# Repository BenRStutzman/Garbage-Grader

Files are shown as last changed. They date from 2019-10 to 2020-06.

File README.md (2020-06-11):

# Garbage Grader

Uses machine learning to score plates of food waste in real time.

Project with Austin Engle for Senior Design.

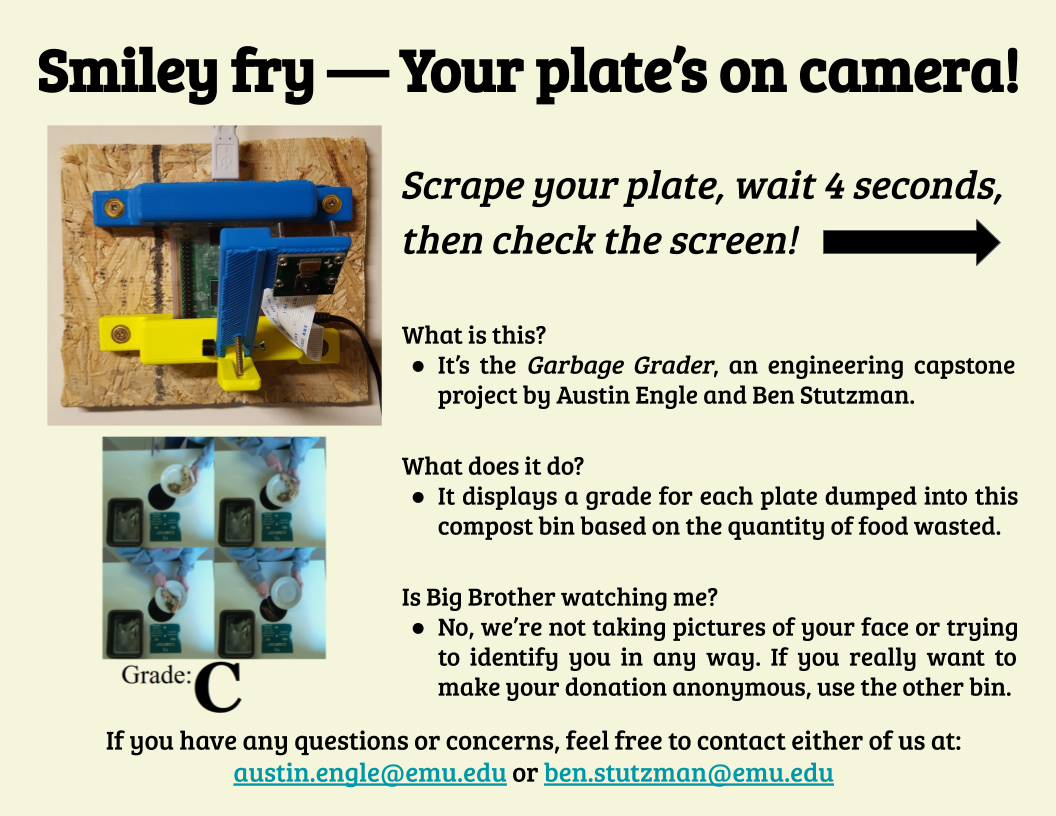
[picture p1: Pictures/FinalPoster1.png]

Poster hanging above the compost bin in EMU's cafeteria
<br><br>
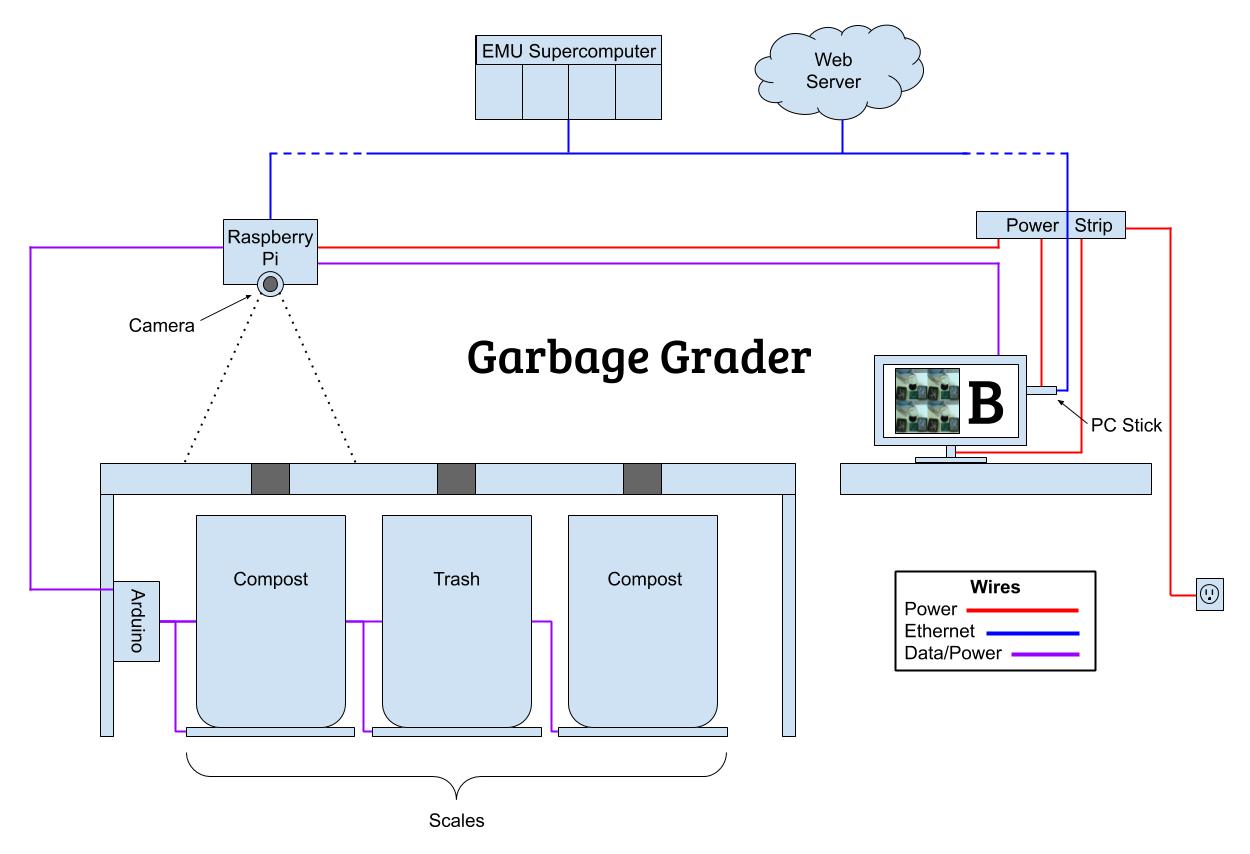
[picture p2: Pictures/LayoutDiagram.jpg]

Overall layout
<br><br>
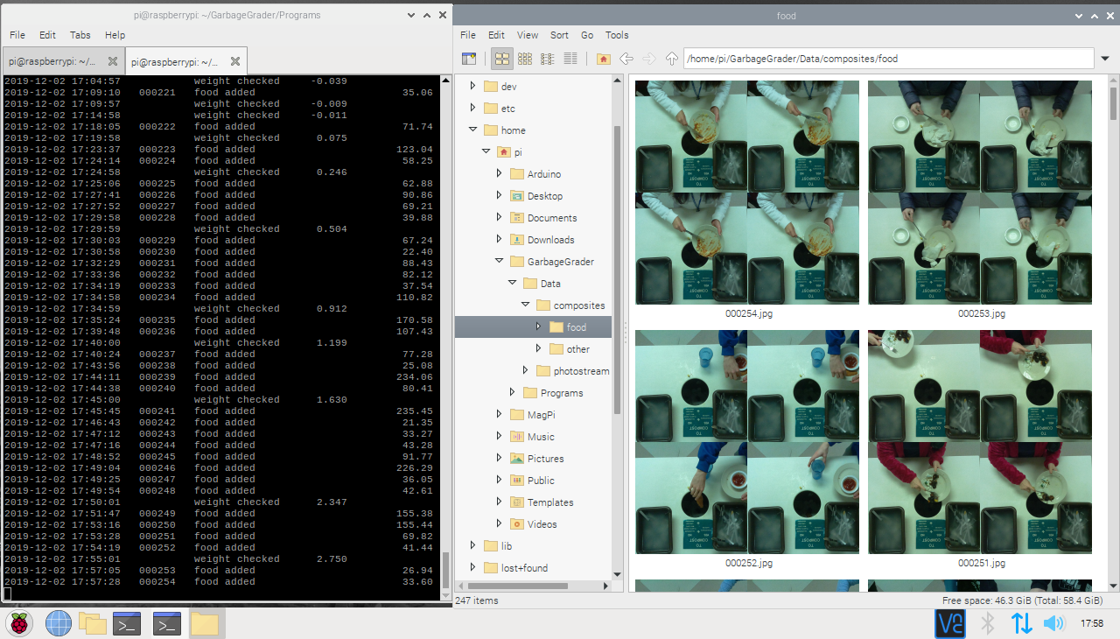
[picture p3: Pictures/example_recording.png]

Raspberry Pi recording pictures of each plate
<br><br>
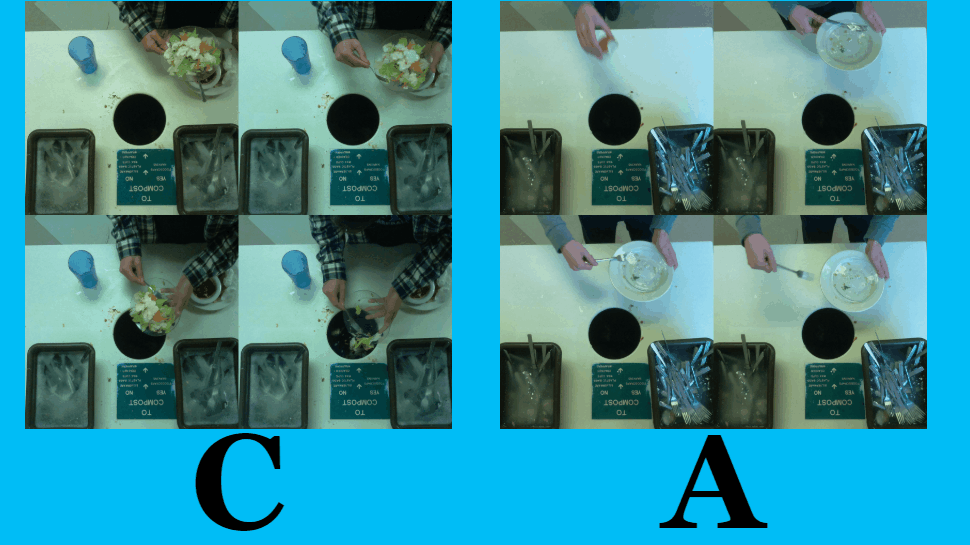
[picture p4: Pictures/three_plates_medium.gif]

Example of TV display as plates are scraped into the compost

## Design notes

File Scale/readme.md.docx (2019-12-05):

To get the arduino code working for the scale, you need to download the hx711 library first. Go to Tools -> mangage libraries -> search for ‘hx711’ and the result should look like this:

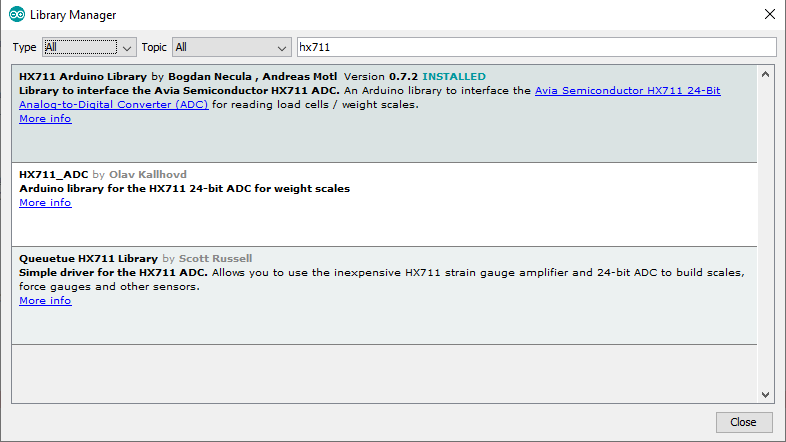
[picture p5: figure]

Select the circled one.

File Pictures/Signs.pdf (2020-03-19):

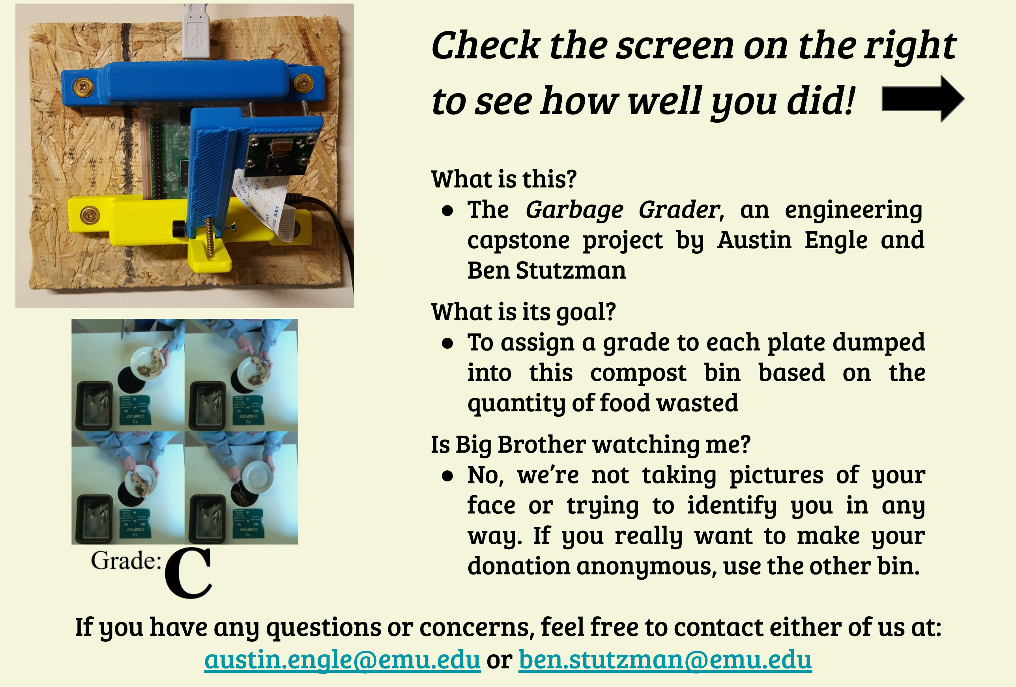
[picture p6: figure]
What is this? ● The Garbage Grader, an engineering capstone project by Austin Engle and Ben Stutzman What is its goal?; into this compost bin based on the quantity of food wasted Is Big Brother watching me? ● No, we’re not taking pictures of your face or trying to identify you in any way. If you really want to make your donation anonymous, use the other bin.; Check the screen on the right to see how well you did!

- To assign a grade to each plate dumped

If you have any questions or concerns, feel free to contact either of us at: austin.engle@emu.edu or ben.stutzman@emu.edu

# Smiley fry — Your plate’s on camera!

- You’ll get a letter grade based on how wasteful our artificial intelligence model thinks your plate was.
- A is the best (no unnecessary waste) and
F is the worst (way too much waste).
- Our model counts all avoidable waste it sees in the picture, including leftover drinks and excess napkins.
- It’s not perfect, but about 93% of the grades it gives are within one letter of what a human would say—and we’re working on improving it.
- If you’re disappointed with your grade:

## Consider taking less food next time!

If you have any questions or concerns, feel free to contact either of us at: austin.engle@emu.edu or ben.stutzman@emu.edu

# What does my grade mean?

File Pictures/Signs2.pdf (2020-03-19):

What is this?
- It’s the Garbage Grader, an engineering capstone project by Austin Engle and Ben Stutzman.

What does it do?
- It displays a grade for each plate dumped into this compost bin based on the quantity of food wasted.

Is Big Brother watching me?
- No, we’re not taking pictures of your face or trying to identify you in any way. If you really want to make your donation anonymous, use the other bin. If you have any questions or concerns, feel free to contact either of us at: austin.engle@emu.edu or ben.stutzman@emu.edu

# Smiley fry — Your plate’s on camera!

Scrape your plate, wait 4 seconds,

### then check the screen!

- You get a letter grade based on how wasteful our artificial intelligence model thinks your plate was.
- A is the best (no unnecessary waste) and
F is the worst (way too much waste).
- Our model counts all avoidable waste it sees in the picture, including leftover drinks and excess napkins.
- It’s not perfect, but about 93% of the grades it gives are within one letter of what a human would say—and we’re working on improving it.
- To improve your grade next time:

## Clean your plate really well

or

## Consider taking less food!

If you have any questions or concerns, feel free to contact either of us at: austin.engle@emu.edu or ben.stutzman@emu.edu

# What does my grade mean?

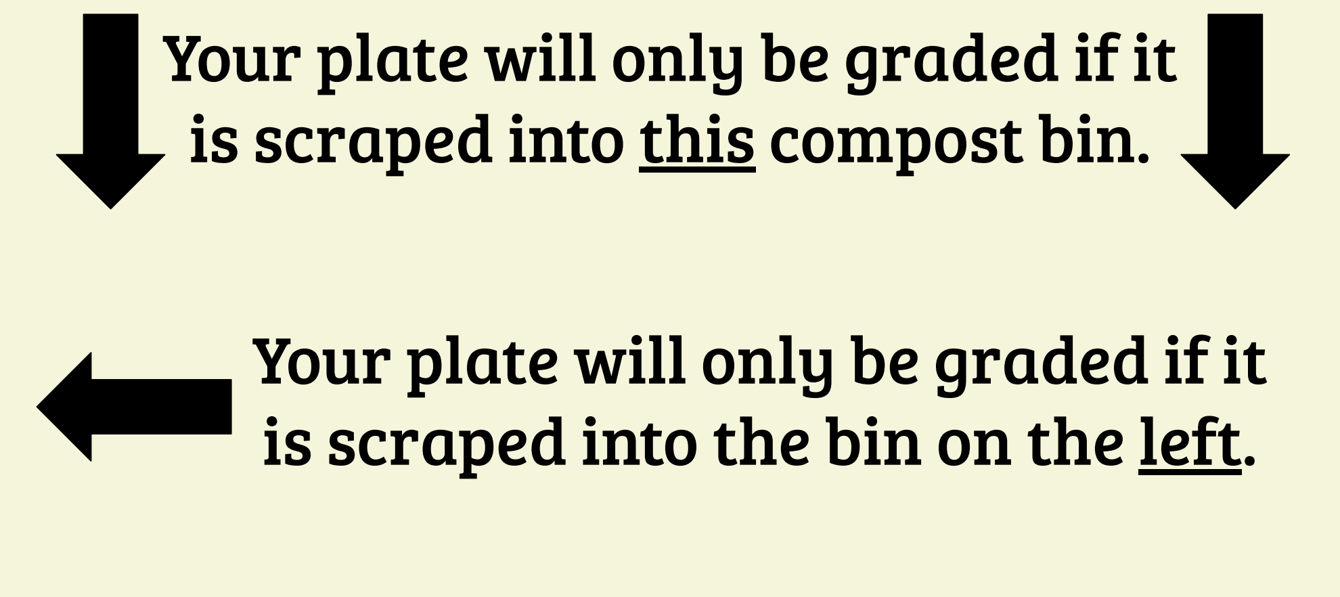
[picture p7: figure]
Your plate will only be graded if it is scraped into this compost bin.; Your plate will only be graded if it is scraped into the bin on the left.

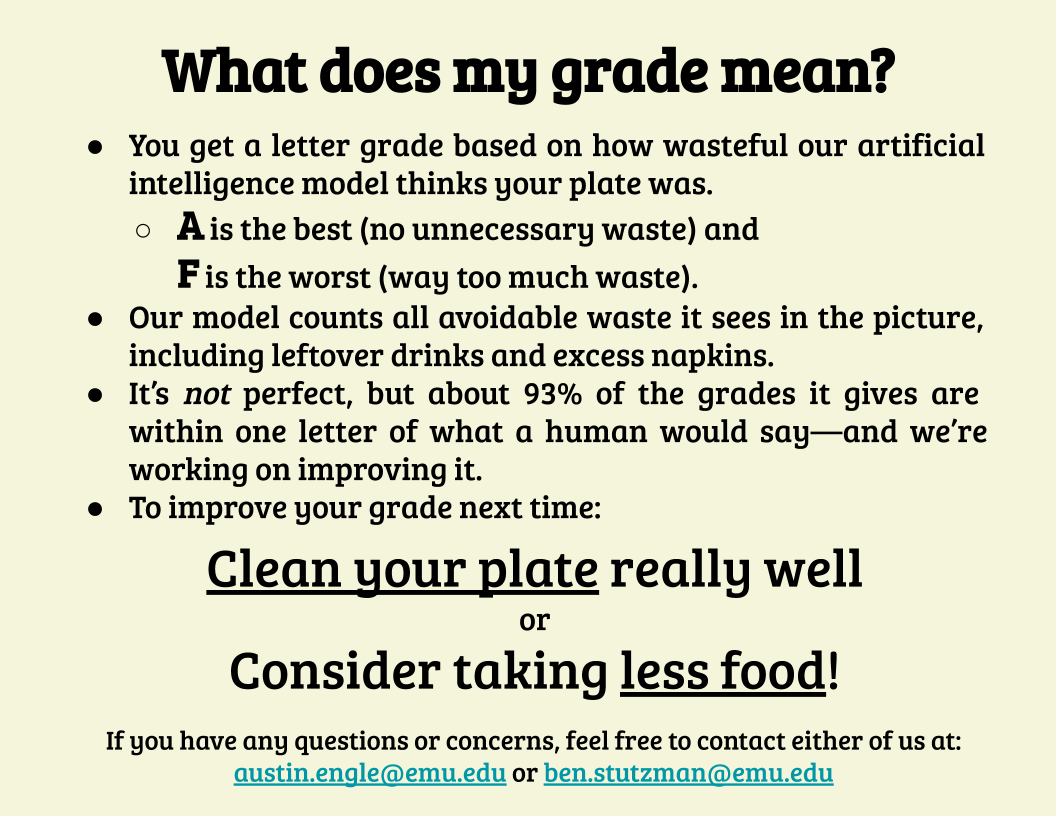
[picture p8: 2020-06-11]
Pictures/FinalPoster2.png

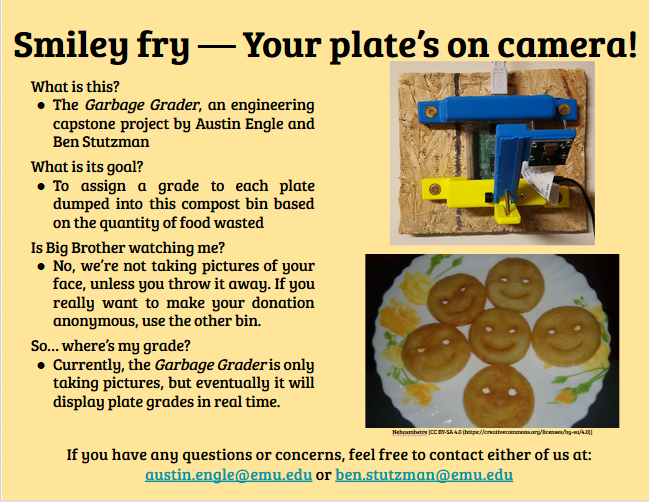
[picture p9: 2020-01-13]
Pictures/poster.png

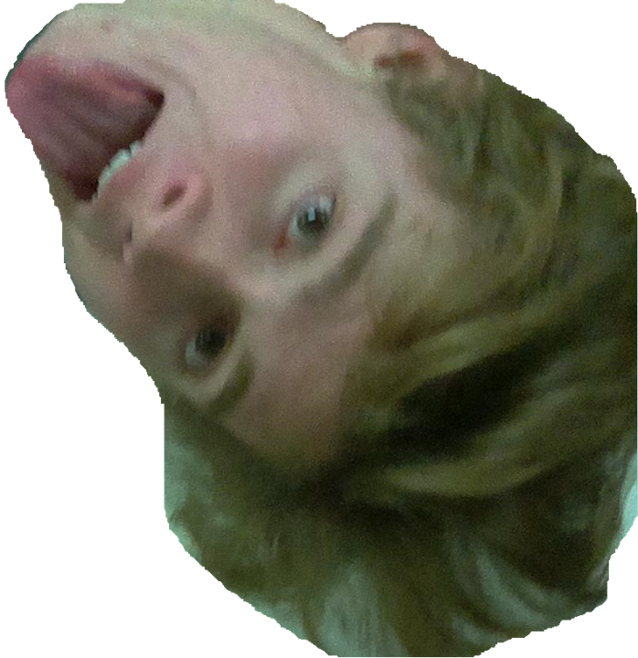
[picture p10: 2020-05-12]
Pictures/Seth_cropped.png

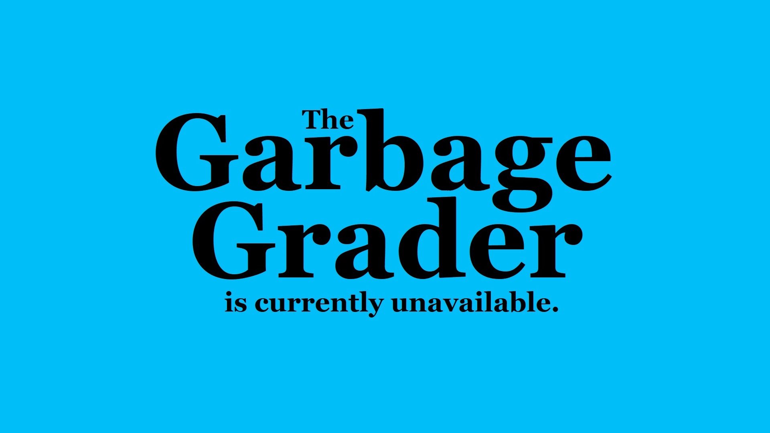
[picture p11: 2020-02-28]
Pictures/ScreenSaver.jpg

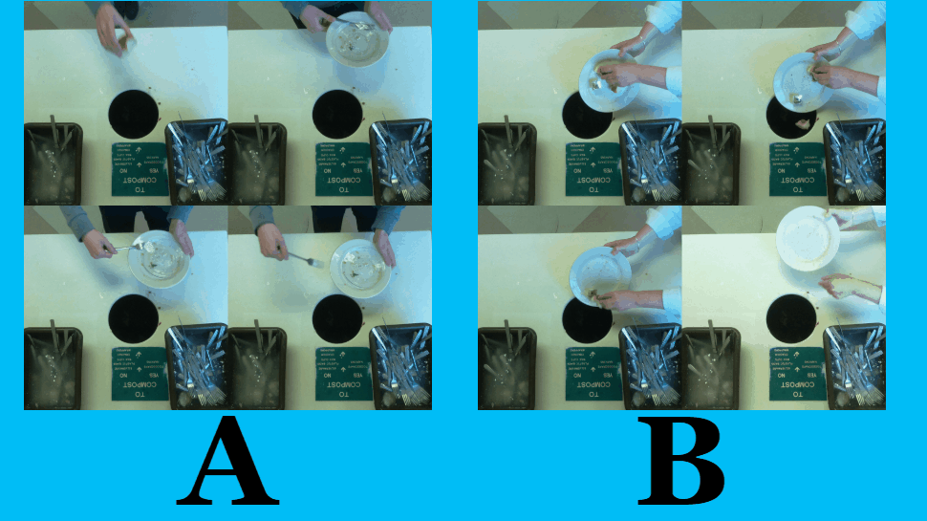
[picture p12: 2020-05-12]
Pictures/new_plate.gif

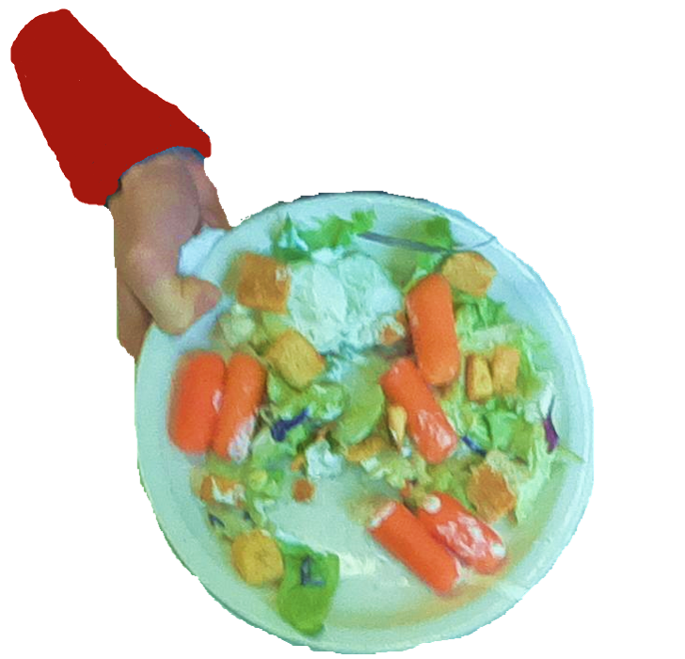
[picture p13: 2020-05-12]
Pictures/cropped_plate_redsleeve.png

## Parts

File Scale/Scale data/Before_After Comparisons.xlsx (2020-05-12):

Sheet: complete_log_2020-02-28
 |  |  |  |  |  |  |  |  |  | Ns excluded |  | < 20g, > 400g, and Ns excluded |  | Grade distribution
Time | ID | Weight | Grade | A_prob | B_prob | C_prob | D_prob | F_prob | N_prob | Weight | Grade | Weight | Grade | Grade | Count | Proportion
2020-02-21 15:43 | 1 | 121 | A | 0.81 | 0.17 | 0.02 | 0 | 0 | 0 | 121 | A | 121 | A | A | 187 | 0.12
2020-02-21 15:45 | 2 | 36 | N | 0.01 | 0 | 0 | 0 | 0 | 0.98 | #N/A | #N/A | #N/A | #N/A | B | 641 | 0.4
2020-02-21 15:45 | 3 | 80 | N | 0 | 0 | 0 | 0 | 0 | 0.99 | #N/A | #N/A | #N/A | #N/A | C | 214 | 0.13
2020-02-21 16:04 | 5 | 75 | C | 0 | 0.08 | 0.53 | 0.19 | 0.2 | 0 | 75 | C | 75 | C | D | 67 | 0.04
2020-02-21 16:04 | 6 | 27 | B | 0.09 | 0.56 | 0.15 | 0.03 | 0.04 | 0.13 | 27 | B | 27 | B | F | 22 | 0.01
2020-02-21 16:14 | 7 | 275 | B | 0.14 | 0.5 | 0.17 | 0.05 | 0.02 | 0.13 | 275 | B | 275 | B | N | 460 | 0.29
2020-02-21 16:14 | 8 | 42 | B | 0.16 | 0.47 | 0.14 | 0.03 | 0.02 | 0.19 | 42 | B | 42 | B
2020-02-21 17:17 | 10 | 45 | B | 0.2 | 0.57 | 0.19 | 0.02 | 0.01 | 0.01 | 45 | B | 45 | B | Total | 1591 | 0.99
2020-02-21 17:17 | 11 | 167 | C | 0.01 | 0.19 | 0.46 | 0.29 | 0.05 | 0 | 167 | C | 167 | C
2020-02-21 17:24 | 12 | 69 | C | 0.03 | 0.41 | 0.47 | 0.1 | 0 | 0 | 69 | C | 69 | C | Ns excluded:
2020-02-21 17:28 | 13 | 24 | C | 0.1 | 0.36 | 0.38 | 0.14 | 0.01 | 0 | 24 | C | 24 | C | Grade | Count | Proportion
2020-02-21 17:33 | 14 | 37 | B | 0.03 | 0.76 | 0.21 | 0 | 0 | 0 | 37 | B | 37 | B | A | 187 | 0.17
2020-02-21 17:38 | 15 | 135 | A | 0.7 | 0.25 | 0.02 | 0 | 0 | 0.02 | 135 | A | 135 | A | B | 641 | 0.57
2020-02-21 17:38 | 16 | 55 | B | 0.09 | 0.83 | 0.07 | 0 | 0 | 0 | 55 | B | 55 | B | C | 214 | 0.19
2020-02-21 17:40 | 17 | 26 | C | 0.01 | 0.24 | 0.45 | 0.26 | 0.03 | 0 | 26 | C | 26 | C | D | 67 | 0.06
2020-02-21 17:40 | 18 | 71 | B | 0.13 | 0.75 | 0.11 | 0.01 | 0 | 0 | 71 | B | 71 | B | F | 22 | 0.02
2020-02-21 17:41 | 19 | 38 | B | 0.32 | 0.45 | 0.17 | 0.05 | 0 | 0 | 38 | B | 38 | B
2020-02-21 17:44 | 20 | 24 | B | 0.07 | 0.87 | 0.06 | 0 | 0 | 0 | 24 | B | 24 | B | Total | 1131 | 1.01
2020-02-21 17:48 | 21 | 164 | A | 0.89 | 0.1 | 0.01 | 0 | 0 | 0 | 164 | A | 164 | A
2020-02-21 17:52 | 22 | 26 | B | 0.18 | 0.58 | 0.17 | 0.07 | 0 | 0 | 26 | B | 26 | B | Ns, < 20g, and > 400g excluded:
2020-02-21 17:54 | 23 | 31 | B | 0.01 | 0.88 | 0.11 | 0 | 0 | 0 | 31 | B | 31 | B | Grade | Count | Proportion
2020-02-21 17:57 | 24 | 100 | A | 0.78 | 0.2 | 0.02 | 0 | 0 | 0 | 100 | A | 100 | A | A | 182 | 0.16
2020-02-21 17:57 | 25 | 21 | B | 0 | 0.96 | 0.04 | 0 | 0 | 0 | 21 | B | 21 | B | B | 634 | 0.57
2020-02-21 17:57 | 26 | 49 | B | 0.15 | 0.79 | 0.05 | 0.01 | 0 | 0.01 | 49 | B | 49 | B | C | 208 | 0.19
2020-02-21 17:59 | 27 | 106 | A | 0.57 | 0.27 | 0.1 | 0.03 | 0.01 | 0.03 | 106 | A | 106 | A | D | 63 | 0.06
2020-02-21 18:02 | 28 | 78 | N | 0 | 0 | 0 | 0 | 0 | 1 | #N/A | #N/A | #N/A | #N/A | F | 18 | 0.02
2020-02-21 18:14 | 29 | 49 | B | 0.26 | 0.62 | 0.09 | 0.01 | 0 | 0.01 | 49 | B | 49 | B
2020-02-21 18:19 | 30 | 38 | C | 0.01 | 0.26 | 0.5 | 0.2 | 0.02 | 0 | 38 | C | 38 | C | Total | 1105 | 1
2020-02-21 18:19 | 31 | 27 | B | 0.01 | 0.53 | 0.39 | 0.06 | 0 | 0 | 27 | B | 27 | B
2020-02-21 18:35 | 32 | 105 | B | 0.03 | 0.63 | 0.32 | 0.02 | 0 | 0 | 105 | B | 105 | B
2020-02-21 18:40 | 33 | 78 | A | 0.62 | 0.33 | 0.03 | 0.01 | 0.01 | 0.01 | 78 | A | 78 | A
2020-02-21 18:41 | 34 | 29 | C | 0.01 | 0.24 | 0.53 | 0.2 | 0.02 | 0 | 29 | C | 29 | C
2020-02-21 18:41 | 35 | 28 | B | 0 | 0.53 | 0.34 | 0.12 | 0.01 | 0 | 28 | B | 28 | B
2020-02-21 18:45 | 36 | 33 | B | 0.15 | 0.45 | 0.11 | 0.04 | 0.01 | 0.25 | 33 | B | 33 | B
2020-02-21 18:47 | 37 | 44 | B | 0.03 | 0.74 | 0.2 | 0.02 | 0 | 0 | 44 | B | 44 | B
2020-02-21 18:47 | 38 | 140 | B | 0.03 | 0.68 | 0.24 | 0.05 | 0 | 0 | 140 | B | 140 | B
2020-02-21 18:57 | 39 | 128 | C | 0.03 | 0.4 | 0.45 | 0.12 | 0.01 | 0 | 128 | C | 128 | C
2020-02-21 18:58 | 40 | 545 | C | 0.01 | 0.12 | 0.54 | 0.28 | 0.05 | 0 | 545 | C | #N/A | #N/A
2020-02-21 19:02 | 41 | 74 | A | 0.75 | 0.17 | 0.03 | 0.01 | 0 | 0.03 | 74 | A | 74 | A
2020-02-21 19:06 | 42 | 32 | B | 0.02 | 0.52 | 0.36 | 0.1 | 0.01 | 0 | 32 | B | 32 | B
2020-02-21 19:06 | 43 | 33 | C | 0.01 | 0.45 | 0.47 | 0.06 | 0 | 0 | 33 | C | 33 | C
2020-02-21 19:10 | 44 | 23 | B | 0.1 | 0.84 | 0.05 | 0.01 | 0 | 0.01 | 23 | B | 23 | B
2020-02-21 19:13 | 45 | 166 | C | 0.01 | 0.17 | 0.7 | 0.12 | 0 | 0 | 166 | C | 166 | C
2020-02-21 19:20 | 46 | 126 | C | 0.01 | 0.29 | 0.53 | 0.16 | 0.01 | 0 | 126 | C | 126 | C
2020-02-21 19:23 | 47 | 1043 | N | 0.01 | 0 | 0 | 0 | 0 | 0.99 | #N/A | #N/A | #N/A | #N/A
2020-02-21 19:32 | 50 | 25 | B | 0.06 | 0.79 | 0.13 | 0.01 | 0 | 0 | 25 | B | 25 | B
2020-02-21 19:33 | 51 | 106 | B | 0.03 | 0.57 | 0.36 | 0.03 | 0 | 0 | 106 | B | 106 | B
2020-02-21 19:35 | 52 | 161 | A | 0.61 | 0.35 | 0.04 | 0 | 0 | 0 | 161 | A | 161 | A
2020-02-21 19:37 | 53 | 216 | D | 0 | 0.03 | 0.4 | 0.51 | 0.06 | 0 | 216 | D | 216 | D
2020-02-21 19:38 | 54 | 32 | N | 0 | 0 | 0 | 0 | 0 | 1 | #N/A | #N/A | #N/A | #N/A
2020-02-21 19:50 | 55 | 176 | C | 0.09 | 0.2 | 0.54 | 0.15 | 0.02 | 0 | 176 | C | 176 | C
2020-02-22 10:02 | 57 | 34 | A | 0.7 | 0.14 | 0.04 | 0.01 | 0 | 0.12 | 34 | A | 34 | A
2020-02-22 10:39 | 58 | 230 | D | 0 | 0.03 | 0.39 | 0.48 | 0.1 | 0 | 230 | D | 230 | D
2020-02-22 10:58 | 59 | 31 | B | 0.11 | 0.69 | 0.15 | 0.03 | 0.01 | 0 | 31 | B | 31 | B
2020-02-22 10:59 | 60 | 202 | B | 0.1 | 0.51 | 0.37 | 0.03 | 0 | 0 | 202 | B | 202 | B
2020-02-22 11:00 | 61 | 137 | B | 0.12 | 0.79 | 0.06 | 0.02 | 0 | 0 | 137 | B | 137 | B
2020-02-22 11:01 | 62 | 64 | B | 0.03 | 0.49 | 0.37 | 0.1 | 0.01 | 0 | 64 | B | 64 | B
2020-02-22 11:01 | 63 | 64 | C | 0.03 | 0.28 | 0.41 | 0.26 | 0.01 | 0 | 64 | C | 64 | C
2020-02-22 11:01 | 64 | 105 | A | 0.66 | 0.32 | 0.01 | 0 | 0 | 0 | 105 | A | 105 | A
2020-02-22 11:02 | 65 | 63 | C | 0 | 0.37 | 0.5 | 0.12 | 0.01 | 0 | 63 | C | 63 | C
2020-02-22 11:02 | 66 | 28 | B | 0.01 | 0.64 | 0.28 | 0.07 | 0.01 | 0 | 28 | B | 28 | B
2020-02-22 11:03 | 67 | 26 | C | 0.02 | 0.3 | 0.32 | 0.19 | 0.17 | 0 | 26 | C | 26 | C
2020-02-22 11:03 | 68 | 122 | C | 0.03 | 0.41 | 0.42 | 0.12 | 0.01 | 0 | 122 | C | 122 | C
2020-02-22 11:05 | 69 | 305 | D | 0 | 0.03 | 0.34 | 0.51 | 0.12 | 0 | 305 | D | #N/A | #N/A
2020-02-22 11:05 | 70 | 163 | B | 0.22 | 0.54 | 0.15 | 0.04 | 0.03 | 0.02 | 163 | B | 163 | B
2020-02-22 11:13 | 71 | 139 | B | 0.36 | 0.43 | 0.12 | 0.08 | 0.01 | 0.01 | 139 | B | 139 | B
2020-02-22 11:16 | 72 | 58 | B | 0.14 | 0.73 | 0.1 | 0.02 | 0 | 0 | 58 | B | 58 | B
2020-02-22 11:19 | 73 | 86 | D | 0.01 | 0.04 | 0.25 | 0.42 | 0.27 | 0 | 86 | D | 86 | D
2020-02-22 11:24 | 74 | 51 | B | 0.3 | 0.62 | 0.06 | 0.02 | 0 | 0 | 51 | B | 51 | B
2020-02-22 11:27 | 75 | 27 | B | 0.03 | 0.61 | 0.28 | 0.08 | 0.01 | 0 | 27 | B | 27 | B
2020-02-22 11:31 | 76 | 88 | B | 0.12 | 0.38 | 0.25 | 0.21 | 0.03 | 0.01 | 88 | B | 88 | B
2020-02-22 11:33 | 77 | 54 | N | 0 | 0 | 0 | 0 | 0 | 0.99 | #N/A | #N/A | #N/A | #N/A
2020-02-22 11:35 | 78 | 47 | N | 0 | 0 | 0 | 0 | 0 | 1 | #N/A | #N/A | #N/A | #N/A
2020-02-22 11:37 | 79 | 156 | B | 0.08 | 0.45 | 0.38 | 0.08 | 0 | 0 | 156 | B | 156 | B
2020-02-22 11:38 | 80 | 80 | N | 0 | 0 | 0 | 0 | 0 | 1 | #N/A | #N/A | #N/A | #N/A
2020-02-22 11:38 | 81 | 120 | N | 0 | 0 | 0 | 0 | 0 | 1 | #N/A | #N/A | #N/A | #N/A
2020-02-22 11:40 | 82 | 110 | B | 0.39 | 0.43 | 0.11 | 0.05 | 0.01 | 0.01 | 110 | B | 110 | B
2020-02-22 11:40 | 83 | 23 | B | 0.05 | 0.9 | 0.03 | 0.01 | 0 | 0 | 23 | B | 23 | B
2020-02-22 11:40 | 84 | 144 | B | 0.13 | 0.6 | 0.12 | 0.04 | 0.01 | 0.11 | 144 | B | 144 | B
2020-02-22 11:41 | 85 | 374 | A | 0.43 | 0.35 | 0.17 | 0.03 | 0.01 | 0.01 | 374 | A | #N/A | #N/A
2020-02-22 11:42 | 86 | 132 | N | 0.33 | 0.05 | 0.01 | 0.01 | 0.01 | 0.6 | #N/A | #N/A | #N/A | #N/A
2020-02-22 11:45 | 87 | 58 | B | 0.24 | 0.56 | 0.14 | 0.03 | 0.01 | 0.03 | 58 | B | 58 | B
2020-02-22 12:04 | 88 | 241 | B | 0.17 | 0.62 | 0.14 | 0.04 | 0.02 | 0.01 | 241 | B | 241 | B
2020-02-22 12:17 | 89 | 22 | B | 0.07 | 0.89 | 0.03 | 0 | 0 | 0 | 22 | B | 22 | B
2020-02-22 12:17 | 90 | 83 | C | 0.07 | 0.28 | 0.4 | 0.22 | 0.02 | 0 | 83 | C | 83 | C
2020-02-22 12:22 | 91 | 65 | B | 0.01 | 0.58 | 0.33 | 0.07 | 0 | 0 | 65 | B | 65 | B
2020-02-22 12:24 | 92 | 35 | B | 0.45 | 0.46 | 0.05 | 0.01 | 0.01 | 0.02 | 35 | B | 35 | B
2020-02-22 12:27 | 93 | 236 | D | 0 | 0.02 | 0.16 | 0.56 | 0.25 | 0 | 236 | D | 236 | D
2020-02-22 12:28 | 94 | 34 | A | 0.51 | 0.24 | 0.06 | 0.05 | 0.02 | 0.13 | 34 | A | 34 | A
2020-02-22 12:28 | 95 | 25 | B | 0.37 | 0.61 | 0.02 | 0 | 0 | 0 | 25 | B | 25 | B
2020-02-22 12:31 | 96 | 124 | D | 0.01 | 0.17 | 0.3 | 0.39 | 0.12 | 0.01 | 124 | D | 124 | D
2020-02-22 12:31 | 97 | 72 | C | 0.11 | 0.28 | 0.34 | 0.24 | 0.02 | 0 | 72 | C | 72 | C
2020-02-22 12:32 | 98 | 98 | D | 0 | 0.03 | 0.29 | 0.56 | 0.13 | 0 | 98 | D | 98 | D
2020-02-22 12:32 | 99 | 51 | C | 0 | 0.05 | 0.51 | 0.42 | 0.02 | 0 | 51 | C | 51 | C
2020-02-22 12:33 | 100 | 87 | A | 0.7 | 0.26 | 0.03 | 0.01 | 0 | 0 | 87 | A | 87 | A
2020-02-22 12:33 | 101 | 39 | B | 0.03 | 0.6 | 0.33 | 0.05 | 0 | 0 | 39 | B | 39 | B
2020-02-22 12:33 | 102 | 26 | B | 0.37 | 0.57 | 0.04 | 0.01 | 0 | 0.01 | 26 | B | 26 | B
2020-02-22 12:34 | 103 | 39 | N | 0.23 | 0.07 | 0.02 | 0.01 | 0.01 | 0.65 | #N/A | #N/A | #N/A | #N/A
2020-02-22 12:37 | 104 | 49 | A | 0.56 | 0.36 | 0.04 | 0.01 | 0.01 | 0.01 | 49 | A | 49 | A
2020-02-22 12:46 | 105 | 24 | A | 0.77 | 0.17 | 0.01 | 0.01 | 0 | 0.03 | 24 | A | 24 | A
2020-02-22 12:47 | 106 | 22 | B | 0.16 | 0.77 | 0.06 | 0.01 | 0 | 0 | 22 | B | 22 | B
2020-02-22 12:48 | 107 | 28 | B | 0.01 | 0.82 | 0.14 | 0.03 | 0 | 0 | 28 | B | 28 | B
2020-02-22 12:48 | 108 | 48 | B | 0.04 | 0.64 | 0.27 | 0.05 | 0 | 0 | 48 | B | 48 | B
2020-02-22 12:50 | 109 | 139 | D | 0 | 0.11 | 0.25 | 0.41 | 0.22 | 0 | 139 | D | 139 | D
2020-02-22 12:52 | 110 | 79 | B | 0.04 | 0.7 | 0.23 | 0.04 | 0 | 0 | 79 | B | 79 | B
2020-02-22 12:52 | 111 | 28 | B | 0.12 | 0.66 | 0.15 | 0.07 | 0 | 0 | 28 | B | 28 | B
2020-02-22 12:53 | 112 | 86 | A | 0.88 | 0.11 | 0.01 | 0 | 0 | 0 | 86 | A | 86 | A
2020-02-22 12:54 | 113 | 27 | A | 0.4 | 0.25 | 0.04 | 0.01 | 0.01 | 0.3 | 27 | A | 27 | A
2020-02-22 12:55 | 114 | 344 | B | 0.25 | 0.37 | 0.31 | 0.06 | 0.01 | 0.01 | 344 | B | #N/A | #N/A
2020-02-22 12:59 | 115 | 110 | B | 0.08 | 0.41 | 0.21 | 0.23 | 0.07 | 0.01 | 110 | B | 110 | B
2020-02-22 13:00 | 116 | 231 | A | 0.64 | 0.34 | 0.02 | 0 | 0 | 0 | 231 | A | 231 | A
2020-02-22 13:03 | 117 | 439 | D | 0.05 | 0.18 | 0.32 | 0.34 | 0.1 | 0.01 | 439 | D | #N/A | #N/A
2020-02-22 13:04 | 118 | 29 | C | 0.04 | 0.4 | 0.41 | 0.14 | 0 | 0 | 29 | C | 29 | C
2020-02-22 13:04 | 119 | 96 | B | 0.41 | 0.46 | 0.11 | 0.02 | 0 | 0 | 96 | B | 96 | B
2020-02-22 13:04 | 120 | 76 | B | 0.04 | 0.45 | 0.35 | 0.14 | 0.02 | 0 | 76 | B | 76 | B
2020-02-22 13:04 | 121 | 71 | B | 0.42 | 0.47 | 0.08 | 0.01 | 0 | 0.02 | 71 | B | 71 | B
2020-02-22 13:11 | 122 | 230 | B | 0.02 | 0.86 | 0.09 | 0.03 | 0 | 0 | 230 | B | 230 | B
2020-02-22 13:12 | 123 | 49 | B | 0.08 | 0.86 | 0.05 | 0.01 | 0 | 0 | 49 | B | 49 | B
2020-02-22 13:13 | 124 | 102 | B | 0.13 | 0.51 | 0.19 | 0.11 | 0.05 | 0.01 | 102 | B | 102 | B
2020-02-22 13:14 | 125 | 248 | C | 0 | 0.3 | 0.65 | 0.04 | 0 | 0 | 248 | C | 248 | C
2020-02-22 13:16 | 126 | 33 | D | 0 | 0.04 | 0.24 | 0.56 | 0.16 | 0 | 33 | D | 33 | D
2020-02-22 13:16 | 127 | 24 | B | 0.16 | 0.77 | 0.06 | 0 | 0 | 0 | 24 | B | 24 | B
2020-02-22 13:20 | 128 | 43 | F | 0 | 0.01 | 0.07 | 0.27 | 0.65 | 0 | 43 | F | 43 | F
2020-02-22 13:20 | 129 | 264 | F | 0 | 0 | 0.05 | 0.39 | 0.56 | 0 | 264 | F | 264 | F
2020-02-22 13:20 | 130 | 363 | D | 0 | 0.01 | 0.15 | 0.62 | 0.22 | 0 | 363 | D | #N/A | #N/A
2020-02-22 16:53 | 131 | 31 | B | 0.03 | 0.57 | 0.3 | 0.09 | 0.01 | 0 | 31 | B | 31 | B
2020-02-22 16:53 | 132 | 62 | B | 0.01 | 0.91 | 0.07 | 0.01 | 0 | 0 | 62 | B | 62 | B
2020-02-22 17:13 | 133 | 42 | F | 0 | 0.02 | 0.1 | 0.42 | 0.46 | 0 | 42 | F | 42 | F
2020-02-22 17:13 | 134 | 31 | B | 0.45 | 0.5 | 0.04 | 0 | 0 | 0 | 31 | B | 31 | B
2020-02-22 17:28 | 135 | 38 | B | 0.07 | 0.79 | 0.13 | 0.01 | 0 | 0 | 38 | B | 38 | B
2020-02-22 17:32 | 136 | 27 | B | 0.02 | 0.56 | 0.35 | 0.06 | 0.01 | 0 | 27 | B | 27 | B
2020-02-22 17:32 | 137 | 23 | B | 0.04 | 0.87 | 0.09 | 0.01 | 0 | 0 | 23 | B | 23 | B
2020-02-22 17:41 | 138 | 29 | B | 0.27 | 0.6 | 0.14 | 0 | 0 | 0 | 29 | B | 29 | B
2020-02-22 17:41 | 139 | 102 | B | 0.08 | 0.66 | 0.22 | 0.04 | 0 | 0 | 102 | B | 102 | B
2020-02-22 17:42 | 140 | 50 | C | 0 | 0.16 | 0.78 | 0.06 | 0 | 0 | 50 | C | 50 | C
2020-02-22 17:42 | 141 | 58 | B | 0.01 | 0.56 | 0.38 | 0.04 | 0 | 0 | 58 | B | 58 | B
2020-02-22 17:45 | 142 | 20 | B | 0.18 | 0.6 | 0.07 | 0.01 | 0.01 | 0.12 | 20 | B | 20 | B
2020-02-22 17:46 | 143 | 27 | B | 0.01 | 0.74 | 0.21 | 0.03 | 0.01 | 0 | 27 | B | 27 | B
2020-02-22 17:46 | 144 | 122 | B | 0.16 | 0.7 | 0.12 | 0.01 | 0 | 0 | 122 | B | 122 | B
2020-02-22 17:46 | 145 | 78 | C | 0.01 | 0.28 | 0.67 | 0.03 | 0 | 0 | 78 | C | 78 | C
2020-02-22 17:52 | 146 | 315 | F | 0 | 0 | 0.01 | 0.18 | 0.8 | 0 | 315 | F | #N/A | #N/A
2020-02-22 17:57 | 147 | 58 | B | 0.25 | 0.61 | 0.12 | 0.01 | 0 | 0 | 58 | B | 58 | B
2020-02-22 17:59 | 148 | 67 | C | 0.01 | 0.36 | 0.5 | 0.12 | 0.02 | 0 | 67 | C | 67 | C
2020-02-22 18:00 | 149 | 118 | C | 0.01 | 0.09 | 0.69 | 0.17 | 0.04 | 0 | 118 | C | 118 | C
2020-02-22 18:03 | 150 | 46 | B | 0.01 | 0.72 | 0.23 | 0.03 | 0 | 0 | 46 | B | 46 | B
2020-02-22 18:06 | 151 | 134 | B | 0.06 | 0.73 | 0.19 | 0.03 | 0 | 0 | 134 | B | 134 | B
2020-02-22 18:08 | 152 | 57 | A | 0.64 | 0.29 | 0.05 | 0.01 | 0 | 0.01 | 57 | A | 57 | A
2020-02-22 18:08 | 153 | 63 | B | 0.28 | 0.67 | 0.05 | 0.01 | 0 | 0 | 63 | B | 63 | B
2020-02-22 18:09 | 154 | 55 | C | 0 | 0.03 | 0.85 | 0.12 | 0 | 0 | 55 | C | 55 | C
2020-02-22 18:25 | 155 | 21 | B | 0.4 | 0.57 | 0.03 | 0 | 0 | 0 | 21 | B | 21 | B
2020-02-22 18:26 | 156 | 108 | C | 0.03 | 0.39 | 0.4 | 0.09 | 0.1 | 0 | 108 | C | 108 | C
2020-02-22 18:30 | 157 | 23 | N | 0.01 | 0 | 0 | 0 | 0 | 0.99 | #N/A | #N/A | #N/A | #N/A
2020-02-22 18:41 | 160 | 25 | N | 0 | 0 | 0 | 0 | 0 | 1 | #N/A | #N/A | #N/A | #N/A
2020-02-23 07:23 | 162 | 24 | N | 0 | 0 | 0 | 0 | 0 | 1 | #N/A | #N/A | #N/A | #N/A
2020-02-23 07:39 | 163 | 30 | N | 0 | 0 | 0 | 0 | 0 | 1 | #N/A | #N/A | #N/A | #N/A
2020-02-23 08:07 | 164 | 27 | N | 0 | 0 | 0 | 0 | 0 | 0.99 | #N/A | #N/A | #N/A | #N/A
2020-02-23 08:22 | 165 | 34 | N | 0 | 0 | 0 | 0 | 0 | 1 | #N/A | #N/A | #N/A | #N/A
2020-02-23 08:28 | 166 | 27 | N | 0 | 0 | 0 | 0 | 0 | 1 | #N/A | #N/A | #N/A | #N/A
2020-02-23 08:32 | 167 | 24 | N | 0.03 | 0 | 0 | 0 | 0 | 0.96 | #N/A | #N/A | #N/A | #N/A
2020-02-23 08:41 | 168 | 21 | N | 0 | 0 | 0 | 0 | 0 | 1 | #N/A | #N/A | #N/A | #N/A
2020-02-23 08:44 | 169 | 31 | N | 0 | 0 | 0 | 0 | 0 | 1 | #N/A | #N/A | #N/A | #N/A
2020-02-23 08:54 | 170 | 136 | A | 0.48 | 0.42 | 0.06 | 0.01 | 0.01 | 0.02 | 136 | A | 136 | A
2020-02-23 08:57 | 171 | 34 | N | 0 | 0 | 0 | 0 | 0 | 1 | #N/A | #N/A | #N/A | #N/A
2020-02-23 08:59 | 172 | 30 | N | 0 | 0 | 0 | 0 | 0 | 1 | #N/A | #N/A | #N/A | #N/A
2020-02-23 09:01 | 173 | 27 | N | 0 | 0 | 0 | 0 | 0 | 1 | #N/A | #N/A | #N/A | #N/A
2020-02-23 09:03 | 174 | 23 | N | 0 | 0 | 0 | 0 | 0 | 1 | #N/A | #N/A | #N/A | #N/A
2020-02-23 09:06 | 175 | 38 | B | 0.38 | 0.41 | 0.1 | 0.03 | 0.01 | 0.07 | 38 | B | 38 | B
2020-02-23 09:09 | 176 | 24 | N | 0 | 0 | 0 | 0 | 0 | 1 | #N/A | #N/A | #N/A | #N/A
2020-02-23 09:11 | 177 | 51 | N | 0 | 0 | 0 | 0 | 0 | 1 | #N/A | #N/A | #N/A | #N/A
2020-02-23 09:13 | 178 | 49 | N | 0 | 0 | 0 | 0 | 0 | 1 | #N/A | #N/A | #N/A | #N/A
2020-02-23 09:15 | 179 | 102 | N | 0 | 0 | 0 | 0 | 0 | 1 | #N/A | #N/A | #N/A | #N/A
2020-02-23 09:17 | 180 | 41 | N | 0 | 0 | 0 | 0 | 0 | 1 | #N/A | #N/A | #N/A | #N/A
2020-02-23 09:20 | 181 | 41 | N | 0 | 0 | 0 | 0 | 0 | 1 | #N/A | #N/A | #N/A | #N/A
2020-02-23 09:22 | 182 | 40 | N | 0 | 0 | 0 | 0 | 0 | 1 | #N/A | #N/A | #N/A | #N/A
2020-02-23 09:30 | 183 | 20 | N | 0 | 0 | 0 | 0 | 0 | 1 | #N/A | #N/A | #N/A | #N/A
2020-02-23 09:32 | 184 | 49 | N | 0 | 0 | 0 | 0 | 0 | 1 | #N/A | #N/A | #N/A | #N/A
2020-02-23 09:34 | 185 | 26 | N | 0 | 0 | 0 | 0 | 0 | 1 | #N/A | #N/A | #N/A | #N/A
2020-02-23 09:36 | 186 | 80 | N | 0 | 0 | 0 | 0 | 0 | 1 | #N/A | #N/A | #N/A | #N/A
2020-02-23 09:39 | 187 | 24 | N | 0 | 0 | 0 | 0 | 0 | 1 | #N/A | #N/A | #N/A | #N/A
2020-02-23 09:41 | 188 | 130 | N | 0 | 0 | 0 | 0 | 0 | 1 | #N/A | #N/A | #N/A | #N/A
2020-02-23 09:43 | 189 | 30 | N | 0.36 | 0.06 | 0.03 | 0.02 | 0.01 | 0.52 | #N/A | #N/A | #N/A | #N/A
2020-02-23 09:45 | 190 | 34 | N | 0 | 0 | 0 | 0 | 0 | 1 | #N/A | #N/A | #N/A | #N/A
2020-02-23 10:10 | 191 | 20 | N | 0.01 | 0 | 0 | 0 | 0 | 0.99 | #N/A | #N/A | #N/A | #N/A
2020-02-23 10:14 | 192 | 26 | N | 0 | 0 | 0 | 0 | 0 | 0.99 | #N/A | #N/A | #N/A | #N/A
2020-02-23 10:22 | 193 | 24 | N | 0 | 0 | 0 | 0 | 0 | 0.99 | #N/A | #N/A | #N/A | #N/A
2020-02-23 11:01 | 194 | 51 | A | 0.41 | 0.38 | 0.03 | 0 | 0 | 0.17 | 51 | A | 51 | A
2020-02-23 11:08 | 195 | 36 | B | 0.22 | 0.26 | 0.25 | 0.2 | 0.04 | 0.02 | 36 | B | 36 | B
2020-02-23 11:18 | 196 | 30 | B | 0.1 | 0.65 | 0.19 | 0.03 | 0.01 | 0.01 | 30 | B | 30 | B
2020-02-23 11:21 | 197 | 33 | N | 0 | 0 | 0 | 0 | 0 | 1 | #N/A | #N/A | #N/A | #N/A
2020-02-23 11:23 | 198 | 49 | N | 0 | 0 | 0 | 0 | 0 | 1 | #N/A | #N/A | #N/A | #N/A
2020-02-23 11:25 | 199 | 43 | N | 0 | 0 | 0 | 0 | 0 | 1 | #N/A | #N/A | #N/A | #N/A
2020-02-23 11:32 | 200 | 29 | B | 0.02 | 0.83 | 0.14 | 0.01 | 0 | 0.01 | 29 | B | 29 | B
2020-02-23 11:35 | 201 | 34 | N | 0 | 0 | 0 | 0 | 0 | 1 | #N/A | #N/A | #N/A | #N/A
2020-02-23 11:37 | 202 | 42 | N | 0 | 0 | 0 | 0 | 0 | 1 | #N/A | #N/A | #N/A | #N/A
2020-02-23 11:39 | 203 | 36 | N | 0.01 | 0 | 0 | 0 | 0 | 0.99 | #N/A | #N/A | #N/A | #N/A
2020-02-23 11:41 | 204 | 47 | N | 0.01 | 0 | 0 | 0 | 0 | 0.99 | #N/A | #N/A | #N/A | #N/A
2020-02-23 11:44 | 205 | 25 | N | 0.01 | 0 | 0 | 0 | 0 | 0.99 | #N/A | #N/A | #N/A | #N/A
2020-02-23 11:46 | 206 | 37 | N | 0.01 | 0 | 0 | 0 | 0 | 0.99 | #N/A | #N/A | #N/A | #N/A
2020-02-23 11:48 | 207 | 31 | N | 0.01 | 0 | 0 | 0 | 0 | 0.99 | #N/A | #N/A | #N/A | #N/A
2020-02-23 11:50 | 208 | 51 | N | 0 | 0 | 0 | 0 | 0 | 1 | #N/A | #N/A | #N/A | #N/A
2020-02-23 11:52 | 209 | 23 | N | 0 | 0 | 0 | 0 | 0 | 1 | #N/A | #N/A | #N/A | #N/A
2020-02-23 11:53 | 210 | 40 | N | 0 | 0 | 0 | 0 | 0 | 1 | #N/A | #N/A | #N/A | #N/A
2020-02-23 11:53 | 211 | 28 | N | 0 | 0 | 0 | 0 | 0 | 1 | #N/A | #N/A | #N/A | #N/A
2020-02-23 11:53 | 212 | 96 | N | 0 | 0 | 0 | 0 | 0 | 1 | #N/A | #N/A | #N/A | #N/A
2020-02-23 11:53 | 213 | 29 | N | 0 | 0 | 0 | 0 | 0 | 1 | #N/A | #N/A | #N/A | #N/A
2020-02-23 11:53 | 214 | 32 | N | 0 | 0 | 0 | 0 | 0 | 1 | #N/A | #N/A | #N/A | #N/A
2020-02-23 11:53 | 215 | 31 | N | 0 | 0 | 0 | 0 | 0 | 1 | #N/A | #N/A | #N/A | #N/A
2020-02-23 11:53 | 216 | 47 | B | 0.21 | 0.74 | 0.04 | 0 | 0 | 0 | 47 | B | 47 | B
2020-02-23 11:54 | 217 | 39 | N | 0.01 | 0 | 0 | 0 | 0 | 0.98 | #N/A | #N/A | #N/A | #N/A
2020-02-23 11:54 | 218 | 20 | N | 0 | 0 | 0 | 0 | 0 | 1 | #N/A | #N/A | #N/A | #N/A
2020-02-23 11:54 | 219 | 31 | N | 0.21 | 0.01 | 0.02 | 0.01 | 0.02 | 0.72 | #N/A | #N/A | #N/A | #N/A
2020-02-23 11:55 | 220 | 37 | B | 0.4 | 0.48 | 0.08 | 0.03 | 0 | 0.01 | 37 | B | 37 | B
2020-02-23 11:55 | 221 | 112 | B | 0.18 | 0.68 | 0.12 | 0.02 | 0 | 0 | 112 | B | 112 | B
2020-02-23 11:56 | 222 | 21 | N | 0 | 0 | 0 | 0 | 0 | 1 | #N/A | #N/A | #N/A | #N/A
2020-02-23 11:58 | 223 | 113 | A | 0.64 | 0.31 | 0.04 | 0.01 | 0 | 0 | 113 | A | 113 | A
2020-02-23 11:59 | 224 | 28 | N | 0.02 | 0 | 0 | 0 | 0 | 0.98 | #N/A | #N/A | #N/A | #N/A
2020-02-23 12:00 | 225 | 79 | B | 0.05 | 0.48 | 0.38 | 0.08 | 0 | 0 | 79 | B | 79 | B
2020-02-23 12:00 | 226 | 41 | A | 0.9 | 0.09 | 0.01 | 0 | 0 | 0 | 41 | A | 41 | A
2020-02-23 12:00 | 227 | 27 | N | 0 | 0 | 0 | 0 | 0 | 1 | #N/A | #N/A | #N/A | #N/A
2020-02-23 12:01 | 228 | 30 | N | 0 | 0 | 0 | 0 | 0 | 1 | #N/A | #N/A | #N/A | #N/A
2020-02-23 12:06 | 229 | 30 | N | 0 | 0 | 0 | 0 | 0 | 0.99 | #N/A | #N/A | #N/A | #N/A
2020-02-23 12:07 | 230 | 35 | N | 0.01 | 0 | 0 | 0 | 0 | 0.99 | #N/A | #N/A | #N/A | #N/A
2020-02-23 12:09 | 231 | 68 | B | 0.11 | 0.68 | 0.17 | 0.03 | 0.01 | 0 | 68 | B | 68 | B
2020-02-23 12:10 | 232 | 26 | A | 0.96 | 0.02 | 0 | 0 | 0 | 0.02 | 26 | A | 26 | A
2020-02-23 12:12 | 233 | 52 | B | 0.43 | 0.49 | 0.06 | 0.01 | 0 | 0 | 52 | B | 52 | B
2020-02-23 12:13 | 234 | 21 | B | 0.11 | 0.53 | 0.19 | 0.15 | 0.02 | 0 | 21 | B | 21 | B
2020-02-23 12:13 | 235 | 32 | B | 0.1 | 0.64 | 0.21 | 0.05 | 0 | 0 | 32 | B | 32 | B
2020-02-23 12:13 | 236 | 176 | B | 0.03 | 0.55 | 0.27 | 0.13 | 0.01 | 0 | 176 | B | 176 | B
2020-02-23 12:13 | 237 | 35 | B | 0.01 | 0.96 | 0.02 | 0 | 0 | 0 | 35 | B | 35 | B
2020-02-23 12:13 | 238 | 31 | N | 0.02 | 0 | 0 | 0 | 0 | 0.97 | #N/A | #N/A | #N/A | #N/A
2020-02-23 12:15 | 239 | 80 | B | 0 | 0.68 | 0.28 | 0.03 | 0 | 0 | 80 | B | 80 | B
2020-02-23 12:15 | 240 | 48 | A | 0.98 | 0.01 | 0 | 0 | 0 | 0 | 48 | A | 48 | A
2020-02-23 12:15 | 241 | 21 | N | 0 | 0 | 0 | 0 | 0 | 1 | #N/A | #N/A | #N/A | #N/A
2020-02-23 12:15 | 242 | 261 | B | 0.01 | 0.6 | 0.31 | 0.07 | 0 | 0 | 261 | B | 261 | B
2020-02-23 12:15 | 243 | 26 | N | 0 | 0 | 0 | 0 | 0 | 1 | #N/A | #N/A | #N/A | #N/A
2020-02-23 12:18 | 244 | 190 | C | 0.06 | 0.32 | 0.5 | 0.11 | 0.01 | 0 | 190 | C | 190 | C
2020-02-23 12:18 | 245 | 44 | B | 0.18 | 0.75 | 0.05 | 0.01 | 0 | 0 | 44 | B | 44 | B
2020-02-23 12:18 | 246 | 184 | D | 0.01 | 0.07 | 0.37 | 0.42 | 0.14 | 0 | 184 | D | 184 | D
2020-02-23 12:18 | 247 | 28 | B | 0 | 0.98 | 0.02 | 0 | 0 | 0 | 28 | B | 28 | B
2020-02-23 12:19 | 248 | 30 | N | 0.01 | 0 | 0 | 0 | 0 | 0.99 | #N/A | #N/A | #N/A | #N/A
2020-02-23 12:19 | 249 | 61 | B | 0.02 | 0.88 | 0.09 | 0.01 | 0 | 0 | 61 | B | 61 | B
2020-02-23 12:19 | 250 | 36 | N | 0 | 0 | 0 | 0 | 0 | 1 | #N/A | #N/A | #N/A | #N/A
2020-02-23 12:20 | 251 | 24 | N | 0.03 | 0.01 | 0 | 0 | 0 | 0.95 | #N/A | #N/A | #N/A | #N/A
2020-02-23 12:20 | 252 | 50 | A | 0.96 | 0.03 | 0 | 0 | 0 | 0 | 50 | A | 50 | A
2020-02-23 12:21 | 253 | 48 | A | 0.54 | 0.4 | 0.05 | 0.01 | 0 | 0 | 48 | A | 48 | A
2020-02-23 12:21 | 254 | 40 | A | 0.72 | 0.27 | 0.01 | 0 | 0 | 0.01 | 40 | A | 40 | A
2020-02-23 12:22 | 255 | 47 | B | 0.22 | 0.44 | 0.18 | 0.11 | 0.02 | 0.03 | 47 | B | 47 | B
2020-02-23 12:23 | 256 | 87 | B | 0.28 | 0.34 | 0.3 | 0.07 | 0.01 | 0.01 | 87 | B | 87 | B
2020-02-23 12:24 | 257 | 23 | N | 0 | 0 | 0 | 0 | 0 | 1 | #N/A | #N/A | #N/A | #N/A
2020-02-23 12:24 | 258 | 215 | C | 0.01 | 0.43 | 0.45 | 0.11 | 0 | 0 | 215 | C | 215 | C
2020-02-23 12:24 | 259 | 47 | N | 0 | 0 | 0 | 0 | 0 | 1 | #N/A | #N/A | #N/A | #N/A
2020-02-23 12:25 | 260 | 27 | N | 0.04 | 0 | 0 | 0 | 0 | 0.96 | #N/A | #N/A | #N/A | #N/A
2020-02-23 12:25 | 261 | 27 | N | 0.01 | 0 | 0 | 0 | 0 | 0.99 | #N/A | #N/A | #N/A | #N/A
2020-02-23 12:26 | 262 | 26 | N | 0 | 0 | 0 | 0 | 0 | 0.99 | #N/A | #N/A | #N/A | #N/A
2020-02-23 12:27 | 263 | 72 | B | 0.05 | 0.44 | 0.28 | 0.2 | 0.03 | 0 | 72 | B | 72 | B
2020-02-23 12:27 | 264 | 32 | A | 0.62 | 0.35 | 0.02 | 0 | 0 | 0.01 | 32 | A | 32 | A
2020-02-23 12:27 | 265 | 21 | N | 0 | 0 | 0 | 0 | 0 | 1 | #N/A | #N/A | #N/A | #N/A
2020-02-23 12:27 | 266 | 24 | N | 0 | 0 | 0 | 0 | 0 | 1 | #N/A | #N/A | #N/A | #N/A
2020-02-23 12:27 | 267 | 41 | A | 0.63 | 0.32 | 0.02 | 0.01 | 0 | 0.02 | 41 | A | 41 | A
2020-02-23 12:28 | 268 | 53 | A | 0.57 | 0.33 | 0.03 | 0.01 | 0 | 0.06 | 53 | A | 53 | A
2020-02-23 12:28 | 269 | 22 | A | 0.96 | 0.04 | 0 | 0 | 0 | 0 | 22 | A | 22 | A
2020-02-23 12:28 | 270 | 25 | N | 0 | 0 | 0 | 0 | 0 | 1 | #N/A | #N/A | #N/A | #N/A
2020-02-23 12:28 | 271 | 53 | B | 0.12 | 0.87 | 0.01 | 0 | 0 | 0 | 53 | B | 53 | B
2020-02-23 12:28 | 272 | 25 | N | 0 | 0 | 0 | 0 | 0 | 1 | #N/A | #N/A | #N/A | #N/A
2020-02-23 12:29 | 273 | 31 | N | 0.01 | 0 | 0 | 0 | 0 | 0.99 | #N/A | #N/A | #N/A | #N/A
2020-02-23 12:29 | 274 | 30 | B | 0.34 | 0.62 | 0.01 | 0 | 0 | 0.02 | 30 | B | 30 | B
2020-02-23 12:31 | 275 | 35 | A | 0.82 | 0.04 | 0 | 0 | 0 | 0.14 | 35 | A | 35 | A
2020-02-23 12:31 | 276 | 26 | N | 0.02 | 0 | 0 | 0 | 0 | 0.98 | #N/A | #N/A | #N/A | #N/A
2020-02-23 12:32 | 277 | 147 | A | 0.6 | 0.38 | 0.02 | 0 | 0 | 0 | 147 | A | 147 | A
2020-02-23 12:32 | 278 | 60 | A | 0.88 | 0.11 | 0 | 0 | 0 | 0.01 | 60 | A | 60 | A
2020-02-23 12:33 | 279 | 66 | A | 0.35 | 0.27 | 0.04 | 0.01 | 0.01 | 0.33 | 66 | A | 66 | A
2020-02-23 12:33 | 280 | 28 | N | 0.03 | 0 | 0 | 0 | 0 | 0.96 | #N/A | #N/A | #N/A | #N/A
2020-02-23 12:34 | 281 | 26 | N | 0 | 0 | 0 | 0 | 0 | 1 | #N/A | #N/A | #N/A | #N/A
2020-02-23 12:34 | 282 | 23 | N | 0 | 0 | 0 | 0 | 0 | 1 | #N/A | #N/A | #N/A | #N/A
2020-02-23 12:34 | 283 | 29 | N | 0 | 0 | 0 | 0 | 0 | 1 | #N/A | #N/A | #N/A | #N/A
2020-02-23 12:35 | 284 | 22 | N | 0 | 0 | 0 | 0 | 0 | 1 | #N/A | #N/A | #N/A | #N/A
2020-02-23 12:36 | 285 | 29 | A | 0.87 | 0.06 | 0 | 0 | 0 | 0.06 | 29 | A | 29 | A
2020-02-23 12:37 | 286 | 29 | N | 0.03 | 0 | 0 | 0 | 0 | 0.96 | #N/A | #N/A | #N/A | #N/A
2020-02-23 12:38 | 287 | 21 | N | 0 | 0 | 0 | 0 | 0 | 1 | #N/A | #N/A | #N/A | #N/A
2020-02-23 12:38 | 288 | 81 | A | 0.57 | 0.39 | 0.03 | 0 | 0 | 0 | 81 | A | 81 | A
2020-02-23 12:38 | 289 | 33 | B | 0.06 | 0.8 | 0.11 | 0.02 | 0 | 0 | 33 | B | 33 | B
2020-02-23 12:38 | 290 | 45 | A | 0.76 | 0.22 | 0.01 | 0 | 0 | 0.02 | 45 | A | 45 | A
2020-02-23 12:40 | 291 | 25 | N | 0.13 | 0.01 | 0 | 0 | 0 | 0.85 | #N/A | #N/A | #N/A | #N/A
2020-02-23 12:40 | 292 | 172 | C | 0 | 0.09 | 0.57 | 0.32 | 0.02 | 0 | 172 | C | 172 | C
2020-02-23 12:40 | 293 | 35 | A | 0.97 | 0.03 | 0 | 0 | 0 | 0 | 35 | A | 35 | A
2020-02-23 12:41 | 294 | 26 | N | 0.1 | 0.01 | 0 | 0 | 0 | 0.88 | #N/A | #N/A | #N/A | #N/A
2020-02-23 12:41 | 295 | 93 | B | 0.1 | 0.83 | 0.05 | 0.01 | 0 | 0.01 | 93 | B | 93 | B
2020-02-23 12:44 | 296 | 23 | N | 0 | 0 | 0 | 0 | 0 | 1 | #N/A | #N/A | #N/A | #N/A
2020-02-23 12:46 | 297 | 28 | B | 0.46 | 0.47 | 0.03 | 0.01 | 0 | 0.01 | 28 | B | 28 | B
2020-02-23 12:46 | 298 | 32 | N | 0 | 0 | 0 | 0 | 0 | 1 | #N/A | #N/A | #N/A | #N/A
2020-02-23 12:48 | 299 | 24 | N | 0 | 0 | 0 | 0 | 0 | 1 | #N/A | #N/A | #N/A | #N/A
2020-02-23 12:48 | 300 | 25 | N | 0 | 0 | 0 | 0 | 0 | 1 | #N/A | #N/A | #N/A | #N/A
2020-02-23 12:48 | 301 | 22 | N | 0 | 0 | 0 | 0 | 0 | 1 | #N/A | #N/A | #N/A | #N/A
2020-02-23 12:50 | 302 | 24 | N | 0 | 0 | 0 | 0 | 0 | 1 | #N/A | #N/A | #N/A | #N/A
2020-02-23 12:50 | 303 | 27 | N | 0 | 0 | 0 | 0 | 0 | 1 | #N/A | #N/A | #N/A | #N/A
2020-02-23 12:50 | 304 | 52 | A | 0.57 | 0.38 | 0.03 | 0.01 | 0 | 0.01 | 52 | A | 52 | A
2020-02-23 12:50 | 305 | 22 | N | 0 | 0 | 0 | 0 | 0 | 1 | #N/A | #N/A | #N/A | #N/A
2020-02-23 12:51 | 306 | 44 | A | 0.92 | 0.06 | 0 | 0 | 0 | 0.01 | 44 | A | 44 | A
2020-02-23 12:53 | 307 | 70 | C | 0 | 0.16 | 0.54 | 0.28 | 0.01 | 0 | 70 | C | 70 | C
2020-02-23 12:53 | 308 | 172 | B | 0.02 | 0.64 | 0.21 | 0.13 | 0.01 | 0 | 172 | B | 172 | B
2020-02-23 12:53 | 309 | 34 | A | 0.98 | 0.02 | 0 | 0 | 0 | 0 | 34 | A | 34 | A
2020-02-23 12:53 | 310 | 34 | N | 0 | 0 | 0 | 0 | 0 | 1 | #N/A | #N/A | #N/A | #N/A
2020-02-23 12:57 | 311 | 23 | N | 0 | 0 | 0 | 0 | 0 | 1 | #N/A | #N/A | #N/A | #N/A
2020-02-23 12:58 | 312 | 23 | N | 0 | 0 | 0 | 0 | 0 | 1 | #N/A | #N/A | #N/A | #N/A
2020-02-23 12:58 | 313 | 48 | A | 0.95 | 0.05 | 0 | 0 | 0 | 0 | 48 | A | 48 | A
2020-02-23 12:58 | 314 | 49 | B | 0.01 | 0.93 | 0.06 | 0 | 0 | 0 | 49 | B | 49 | B
2020-02-23 12:59 | 315 | 26 | N | 0 | 0 | 0 | 0 | 0 | 1 | #N/A | #N/A | #N/A | #N/A
2020-02-23 12:59 | 316 | 31 | N | 0.18 | 0.01 | 0.01 | 0.01 | 0.01 | 0.79 | #N/A | #N/A | #N/A | #N/A
2020-02-23 12:59 | 317 | 35 | N | 0 | 0 | 0 | 0 | 0 | 1 | #N/A | #N/A | #N/A | #N/A
2020-02-23 13:00 | 318 | 39 | A | 0.93 | 0.07 | 0 | 0 | 0 | 0 | 39 | A | 39 | A
2020-02-23 13:01 | 319 | 31 | A | 0.53 | 0.43 | 0.03 | 0.01 | 0 | 0 | 31 | A | 31 | A
2020-02-23 13:01 | 320 | 36 | A | 0.71 | 0.26 | 0.01 | 0 | 0 | 0 | 36 | A | 36 | A
2020-02-23 13:02 | 321 | 36 | N | 0 | 0 | 0 | 0 | 0 | 0.99 | #N/A | #N/A | #N/A | #N/A
2020-02-23 13:02 | 322 | 37 | N | 0 | 0 | 0 | 0 | 0 | 1 | #N/A | #N/A | #N/A | #N/A
2020-02-23 13:03 | 323 | 32 | N | 0 | 0 | 0 | 0 | 0 | 1 | #N/A | #N/A | #N/A | #N/A
2020-02-23 13:04 | 324 | 76 | A | 0.48 | 0.41 | 0.07 | 0.03 | 0 | 0.01 | 76 | A | 76 | A
2020-02-23 13:04 | 325 | 46 | N | 0.01 | 0 | 0 | 0 | 0 | 0.99 | #N/A | #N/A | #N/A | #N/A
2020-02-23 13:05 | 326 | 32 | A | 0.66 | 0.26 | 0.01 | 0 | 0 | 0.07 | 32 | A | 32 | A
2020-02-23 13:07 | 327 | 78 | A | 0.38 | 0.38 | 0.13 | 0.08 | 0.02 | 0.01 | 78 | A | 78 | A
2020-02-23 13:07 | 328 | 36 | A | 0.71 | 0.24 | 0.02 | 0.01 | 0 | 0.02 | 36 | A | 36 | A
2020-02-23 13:08 | 329 | 51 | N | 0.07 | 0.02 | 0 | 0 | 0 | 0.91 | #N/A | #N/A | #N/A | #N/A
2020-02-23 13:08 | 330 | 24 | N | 0 | 0 | 0 | 0 | 0 | 1 | #N/A | #N/A | #N/A | #N/A
2020-02-23 13:08 | 331 | 41 | N | 0 | 0 | 0 | 0 | 0 | 1 | #N/A | #N/A | #N/A | #N/A
2020-02-23 13:10 | 332 | 23 | N | 0 | 0 | 0 | 0 | 0 | 1 | #N/A | #N/A | #N/A | #N/A
2020-02-23 13:14 | 333 | 49 | A | 0.81 | 0.17 | 0.01 | 0 | 0 | 0.01 | 49 | A | 49 | A
2020-02-23 13:18 | 334 | 211 | D | 0 | 0.03 | 0.21 | 0.53 | 0.23 | 0 | 211 | D | 211 | D
2020-02-23 13:20 | 335 | 66 | N | 0 | 0 | 0 | 0 | 0 | 1 | #N/A | #N/A | #N/A | #N/A
2020-02-23 13:22 | 336 | 167 | N | 0 | 0 | 0 | 0 | 0 | 1 | #N/A | #N/A | #N/A | #N/A
2020-02-23 13:24 | 337 | 23 | N | 0 | 0 | 0 | 0 | 0 | 1 | #N/A | #N/A | #N/A | #N/A
2020-02-23 13:27 | 338 | 27 | N | 0 | 0 | 0 | 0 | 0 | 1 | #N/A | #N/A | #N/A | #N/A
2020-02-23 13:29 | 339 | 32 | N | 0 | 0 | 0 | 0 | 0 | 1 | #N/A | #N/A | #N/A | #N/A
2020-02-23 13:31 | 340 | 32 | N | 0 | 0 | 0 | 0 | 0 | 1 | #N/A | #N/A | #N/A | #N/A
2020-02-23 13:33 | 341 | 27 | N | 0 | 0 | 0 | 0 | 0 | 1 | #N/A | #N/A | #N/A | #N/A
2020-02-23 13:36 | 342 | 30 | N | 0 | 0 | 0 | 0 | 0 | 1 | #N/A | #N/A | #N/A | #N/A
2020-02-23 13:42 | 343 | 28 | N | 0 | 0 | 0 | 0 | 0 | 1 | #N/A | #N/A | #N/A | #N/A
2020-02-23 13:45 | 344 | 30 | N | 0 | 0 | 0 | 0 | 0 | 1 | #N/A | #N/A | #N/A | #N/A
2020-02-23 13:47 | 345 | 20 | N | 0 | 0 | 0 | 0 | 0 | 1 | #N/A | #N/A | #N/A | #N/A
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

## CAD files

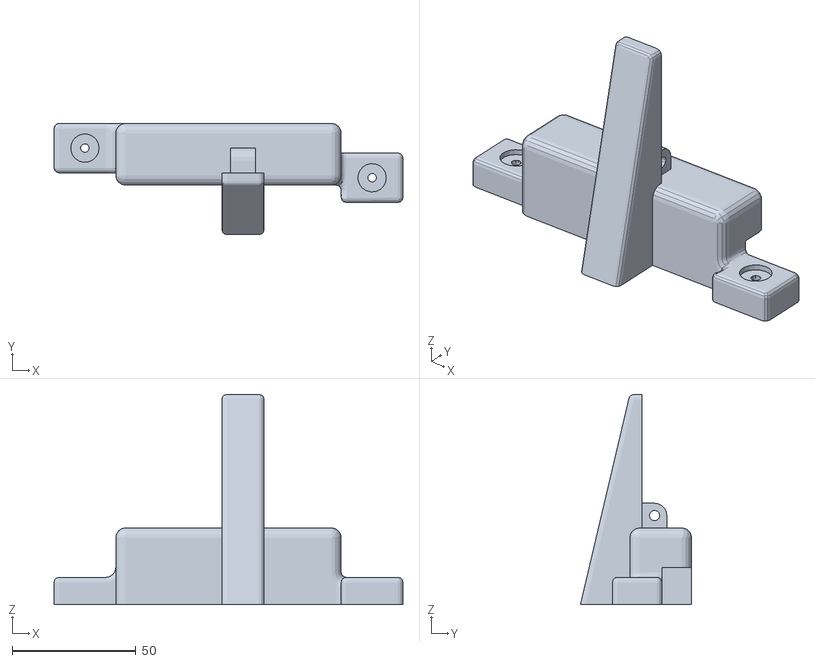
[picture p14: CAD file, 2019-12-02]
3D Printed Parts/Bottom Bracket.stl
141.2 x 45.0 x 85.0

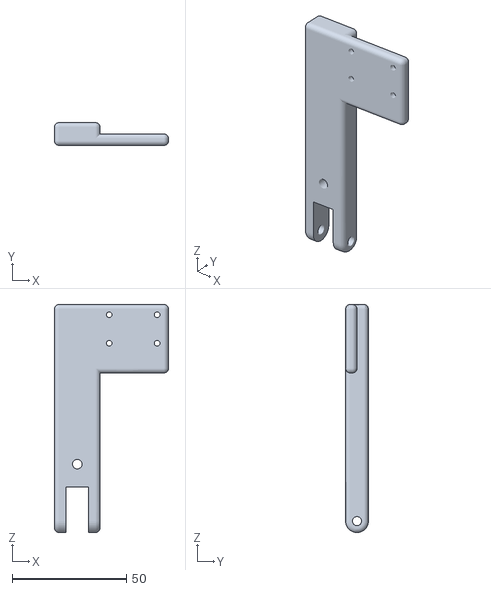
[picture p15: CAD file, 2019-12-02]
3D Printed Parts/Lever.stl
50.0 x 10.0 x 100.0

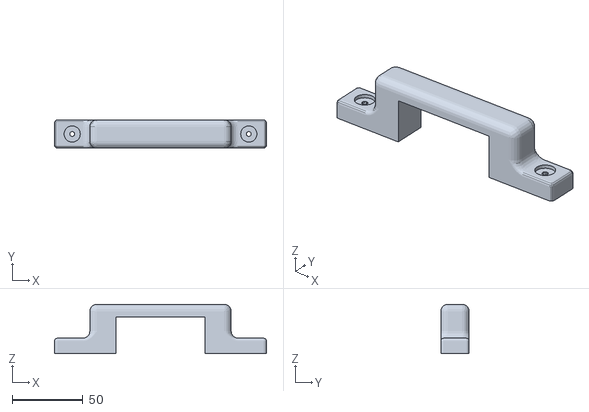
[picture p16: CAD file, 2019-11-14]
3D Printed Parts/Top Bracket.stl
150.0 x 20.0 x 35.0

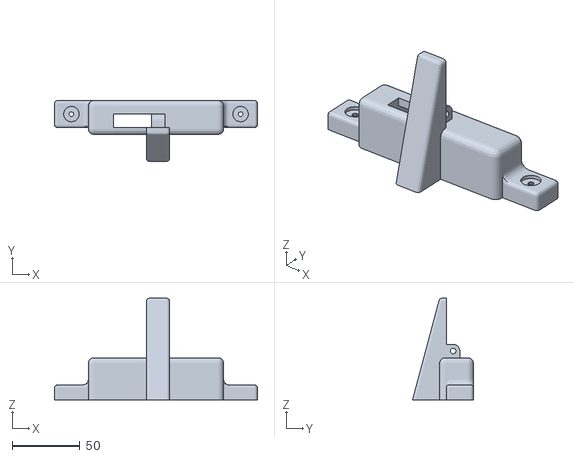
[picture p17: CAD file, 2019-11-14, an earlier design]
3D Printed Parts/Old/Bottom Bracket.stl
150.0 x 45.0 x 75.0

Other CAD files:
3D Printed Parts/Old/Lever.stl
3D Printed Parts/Bottom Bracket.ipt
3D Printed Parts/Lower Assembly.iam
3D Printed Parts/M4 Bolt.ipt
3D Printed Parts/Old/Lower Assembly.iam
3D Printed Parts/Old/blah.ipt
3D Printed Parts/Old/fakeM4Bolt.ipt
3D Printed Parts/Old/lever.ipt
3D Printed Parts/Top Bracket.ipt
3D Printed Parts/blah.ipt
3D Printed Parts/fakeM4Bolt.ipt
3D Printed Parts/lever.ipt

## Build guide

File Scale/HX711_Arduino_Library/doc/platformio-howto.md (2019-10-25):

# PlatformIO howto

https://platformio.org/

List installed platforms

    platformio platform list

List available boards

    platformio boards

Run specific build

    platformio ci --board=megaatmega2560 --lib="." examples/HX711_full_example

Run specific environment

    platformio run --environment lopy4

Build all environments

    platformio run

"Make clean" for all environments

    platformio run -t clean

Dump specific build environment

    platformio run --environment lopy4 --target envdump

See slot `CPPDEFINES`.

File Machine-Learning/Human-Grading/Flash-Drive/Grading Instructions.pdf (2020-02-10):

Instructions for grading food waste pictures

Step 1: Look at the picture and judge whether anything is being disposed at all.
- If nothing is being disposed (e.g. just people walking by, counter being wiped, trash bin being moved, no action at all in picture), give the grade of N for 'not gradeable' and skip the remaining steps.
- If something is being disposed (even if there’s no plate in the picture), continue to step 2.
Step 2: Estimate the total volume (in 8-oz cups) of avoidable waste in the picture.
- This includes combining waste from multiple plates, multiple people, liquids, etc: add up all avoidable waste in the picture.
- This does not include things like fruit peels and chicken bones, and up to one napkin per picture (i.e. everyone gets one 'free' napkin before it starts counting as waste).
Step 3: Judge where the total volume of avoidable waste (V) falls on this scale:
A: | V = 0 cups
B: 0 cups < V ≤ ½ cup
C: ½ cup < V ≤ 1 cup
D: 1 cup < V ≤ 2 cups
F: 2 cups < V
- Give the corresponding letter grade.
- Tips:
- ½ cup is about the size of a hockey puck.
- 1 cup is about the size of a baseball.
Step 4: If you are confused and think the picture presents something new that hasn't been considered (i.e. doesn't fall under N, A, B, C, D, or F), give a longer message explaining your confusion instead of a grade.

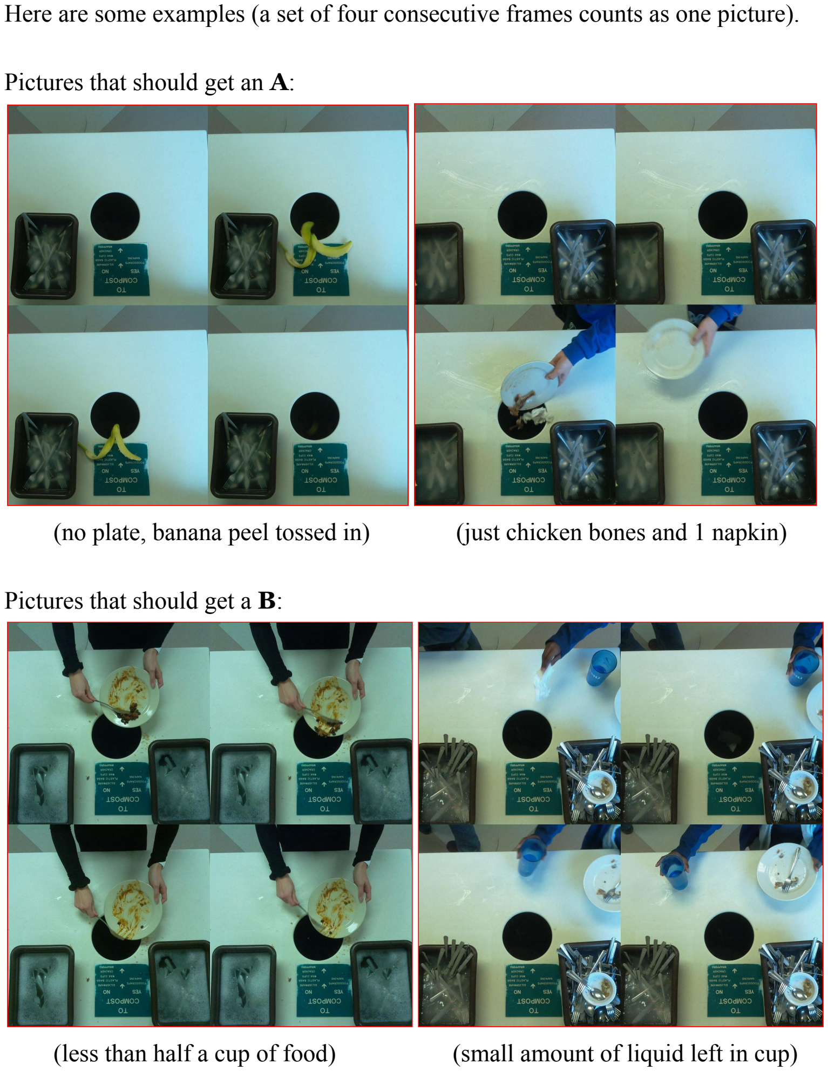
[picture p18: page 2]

Here are some examples (a set of four consecutive frames counts as one picture).

Pictures that should get an A:

(no plate, banana peel tossed in) | (just chicken bones and 1 napkin)

Pictures that should get a B:

(less than half a cup of food) | (small amount of liquid left in cup)

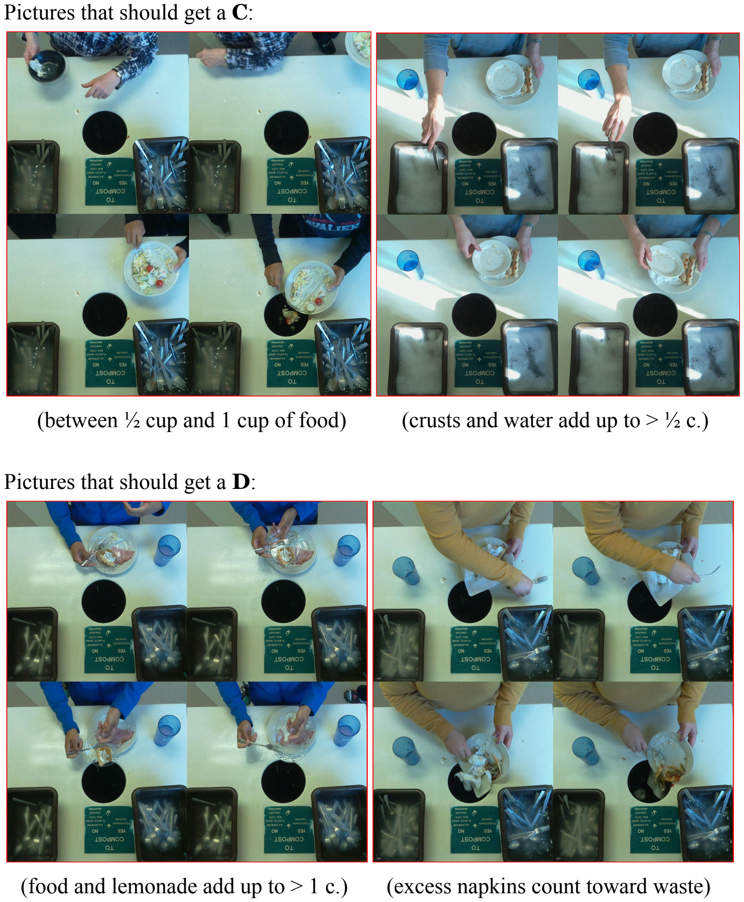
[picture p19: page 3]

Pictures that should get a C:

(between ½ cup and 1 cup of food) (crusts and water add up to > ½ c.)

Pictures that should get a D:

(food and lemonade add up to > 1 c.) (excess napkins count toward waste)

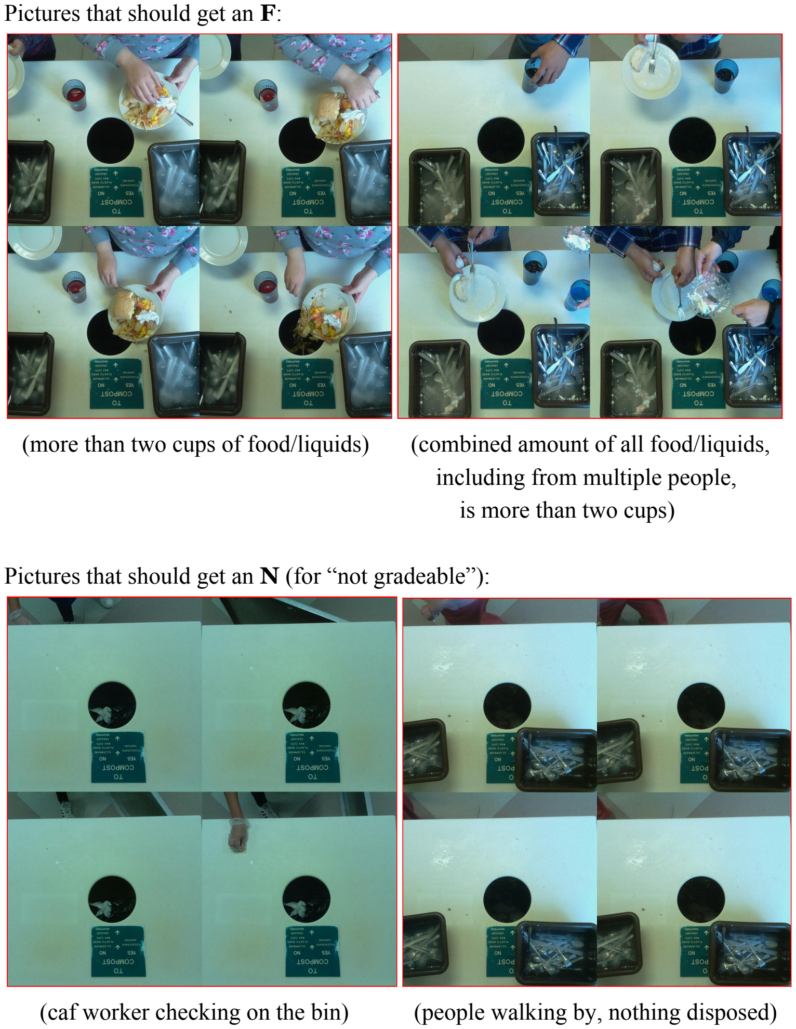
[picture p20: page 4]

Pictures that should get an F:

(more than two cups of food/liquids) (combined amount of all food/liquids, including from multiple people, is more than two cups)

Pictures that should get an N (for “not gradeable”):

(caf worker checking on the bin) (people walking by, nothing disposed)

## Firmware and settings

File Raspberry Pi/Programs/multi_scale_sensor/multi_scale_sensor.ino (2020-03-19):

#include "HX711.h"
#define DOUT_CAM     3
#define CLK_CAM      2
#define DOUT_MIDDLE  5
#define CLK_MIDDLE   4
#define DOUT_FAR     8
#define CLK_FAR      7

#define calibration_factor_1 -20690.0 //This value is obtained using the SparkFun_HX711_Calibration sketch (or just by testing weights in this program and adjusting)
#define calibration_factor_2 -21430.0
#define calibration_factor_3 -24170.0

const byte num_readings = 20; //how many readings at a time it averages
const byte num_avgs = 20; //how many averages back it compares for a "delta"
const int start_delay = 300; //startup time, in cycles, which are about 0.1 seconds
const int dump_time = 1000; //time it waits before assuming a person's done dumping, in ms
const float sensitivity = 0.010; //in kg, the lightest weight it will detect
const float bin_weight = 10; //in kg
const byte check_freq = 5; //in minutes, how often it checks the total weight of the scales

boolean bin_removed;
boolean find_weight;
boolean minor_scale_setup = false;
int num_minor_scale_measure = 0;
long check_interval = check_freq * 60000 - 2000;
unsigned long counter;
unsigned long last_trigger;
unsigned long last_check;
float last_readings[num_readings];
float last_avgs[num_avgs];
float reading;
float avg;
float sum;
float sum_trash;
float sum_far;
float delta;
float item_weight;
float prev_avg;
float max_weight[2];

HX711 scale;
HX711 scale_trash;
HX711 scale_far;


void take_reading() {
  reading = scale.get_units();
  sum -= last_readings[counter % num_readings];
  sum += reading;
  avg = sum / num_readings;
  delta = avg - last_avgs[counter % num_avgs];


  // only record the data from the other scales if we are about to report the data
  // happens for 2 sec every check_freq minutes
  if(minor_scale_setup){
   sum_trash += scale_trash.get_units();
   sum_far += scale_far.get_units();
   num_minor_scale_measure++;
  }
}

void detect_food() {
  if (delta > sensitivity && find_weight == false) {
    Serial.println("food added");
    //Serial.println();
    prev_avg = last_avgs[counter % num_avgs];
    find_weight = true;
    item_weight = delta;
    last_trigger = millis();
  }
}

void measure_weight() {
  if (find_weight) {
    if (delta > sensitivity) { last_trigger = millis(); }
    if (long(millis() - last_trigger) < dump_time) {
      if (avg - prev_avg > item_weight) { item_weight = avg - prev_avg; }
    } else {
      Serial.println(item_weight * 1000, 2);
      //Serial.println();
      find_weight = false;
      reset_readings();
    }
  }
}

void reset_scale() {
  if (not bin_removed) { Serial.println("scale reset"); }
  for(int i = 0; i < start_delay; i++) { scale.get_units(); }
  if (bin_removed) {
    float amount_removed = max_weight[0] - scale.get_units();
    if (amount_removed < 0.1) { Serial.println(0, 3); }
    else { Serial.println(amount_removed, 3); }
  }
  scale.tare();
  reset_readings();
  counter = 1;
  max_weight[0] = 0.0;
  max_weight[1] = 0.0;
  find_weight = false;
  if (bin_removed) {
    Serial.println("scale reset");
    bin_removed = false;
  }
  Serial.println(reading, 3);
}

void zero_scales() {
  Serial.println("scales reset");
  for(int i = 0; i < start_delay; i++) {
    scale.get_units();
    scale_trash.get_units();
    scale_far.get_units();
  }
  scale.tare();
  scale_trash.tare();
  scale_far.tare();
  
  reset_readings();
  counter = 1;
  max_weight[0] = 0.0;
  max_weight[1] = 0.0;
  find_weight = false;
  Serial.println(reading, 3);
}

void reset_readings() {
  
  reading = scale.get_units();
  for (int i = 0; i < num_readings; i++) {
    last_readings[i] = reading;
    last_avgs[i] = reading;
  }
  sum = reading * num_readings;
  
}

void detect_removal() {
  if (avg < -bin_weight / 2 && !find_weight) {
    //if (find_weight) { Serial.println("0.00"); }
    Serial.println("bin removed");
    int i = 0;
    while (i < start_delay) {
      //Serial.println("delta:");
      //Serial.println(delta, 3);
      take_reading();
      last_readings[counter % num_readings] = reading;
      last_avgs[counter % num_avgs] = avg;
      counter++;
      if (delta < -sensitivity) {
        i = 0;
      } else { i++; }
    }
    float base_weight = avg;
    bin_removed = true;
    while (true) {
      while (avg < base_weight + bin_weight / 2 && avg < -bin_weight / 2) {
        //Serial.println(avg, 3);
        take_reading();
        last_readings[counter % num_readings] = reading;
        last_avgs[counter % num_avgs] = avg;
        counter++;
      }
      for (int i = 0; i < 100; i++) {
        take_reading();
        last_readings[counter % num_readings] = reading;
        last_avgs[counter % num_avgs] = avg;
        counter++;
      }
      if (avg > base_weight + bin_weight / 2 || avg > -bin_weight / 2) {
        break;
      }
    }
    reset_scale();
  }
}

void occasional_checks() {
  // stuff to check every check_freq minutes
  if (millis() - last_check >= check_interval) {
    // check to see if we need to premptively need to start recording data from the other scales
    if(!minor_scale_setup){
      last_check += 2000;
      minor_scale_setup = true;
    }
    else {
      // Camera's Scale
      Serial.println("weight 1 checked");
      Serial.println(avg, 3);
  
      // Other Scales (Middle and Far)
      Serial.println("weight 2 checked");
      Serial.println(sum_trash/num_minor_scale_measure, 3);
      
      Serial.println("weight 3 checked");
      Serial.println(sum_far/num_minor_scale_measure,3);

      // reset the vars used for printing the minor scales weight
      sum_trash = 0;
      sum_far = 0;
      num_minor_scale_measure = 0;
      minor_scale_setup = false;

      
      // Stuff to make sure that this can continue working
      last_check += check_interval;
      max_weight[0] = max_weight[1];
      max_weight[1] = avg;
      //String input = Serial.readString();
      //Serial.println(input);
      if (Serial.readString() == "zero scales") {
        zero_scales();
      }
    }
  }
}

void setup() {
  Serial.begin(9600);

  pinMode(9,OUTPUT);
  digitalWrite(9,HIGH);     // This is so that we can have other ports as 5V for the other
  pinMode(10,OUTPUT);       // scales.
  digitalWrite(10 ,HIGH);  

  scale_trash.begin(DOUT_MIDDLE, CLK_MIDDLE);
  scale_trash.set_scale(calibration_factor_2); //This value is obtained by using the SparkFun_HX711_Calibration sketch

  scale_far.begin(DOUT_FAR, CLK_FAR);
  scale_far.set_scale(calibration_factor_3); //This value is obtained by using the SparkFun_HX711_Calibration sketch

  scale.begin(DOUT_CAM, CLK_CAM);
  scale.set_scale(calibration_factor_1); //This value is obtained by using the SparkFun_HX711_Calibration sketch
  
  zero_scales();

}

void loop() {

//  Serial.println("made it here");
  occasional_checks();
  detect_removal();
  take_reading();
  detect_food();
  measure_weight();

  last_readings[counter % num_readings] = reading;
  last_avgs[counter % num_avgs] = avg;
  counter++;
  
  /*Serial.println(delta, 3);

  /*
  //Stuff To print for diagnosis
  Serial.print("Reading: ");
  if (reading > 0) { Serial.print(" "); }
  Serial.print(reading, 4); Serial.print(" kg");
  Serial.print("   Moving avg: ");
  if (avg > 0) { Serial.print(" "); }
  Serial.print(avg, 4); Serial.print(" kg");
  Serial.print("   Delta: ");
  if (delta > 0) { Serial.print(" "); }
  Serial.print(delta * 1000, 1); Serial.print(" g");
  Serial.println();
  */
  
  
}

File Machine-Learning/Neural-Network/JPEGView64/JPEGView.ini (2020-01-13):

[JPEGView]

; IMPORTANT NOTICE
; ================
; This global INI file is normally located in the same directory as the JPEGView executable.
; Its settings can be overridden on a per user basis by placing a JPEGView.ini file in the
; %APPDATA%\JPEGView\ folder. Settings not present in the user's INI file are read from this global INI file.
; The "Save parameters to INI" and "Edit user settings" menu commands will write the settings to the user
; INI file and not to the global!
; For installations on a USB memory stick, JPEGView can be forced to store its settings and the
; parameter DB in the EXE path by setting the StoreToEXEPath key to true.


; Only set this to true if writing to the EXE directory makes sense, e.g. on an installation on
; an USB memory stick. Never set it to true when the EXE is located in the 'Program Files' folder,
; with Windows versions newer than Windows XP this would not work!
StoreToEXEPath=false

; Language used in the user interface. Set to 'auto' to use the language of the operating system.
; Other languages must use the ISO 639-1 language code (two letters)
; Currently supported:
; 'en'    English (default)
; 'es'    Spanish (Spain)
; 'es-ar' Spanish (latinoamerica)
; 'pt-br' Portuguese (Brasil)
; 'pt'    Portuguese
; 'de'    German
; 'it'    Italian
; 'fr'    French
; 'zh'    Chinese
; 'zh-tw' Chinese (Taiwan)
; 'ja'    Japanese
; 'kr'    Korean
; 'ro'    Romanian
; 'ru'    Russian
; 'sv'    Swedish
; 'cs'    Czech
; 'el'    Greek
; 'eu'    Basque
; 'bel'   Belorussian
; 'uk'    Ukrainian
; 'pl'    Polish
Language=auto

; File endings of files to be decoded by WIC (Windows Image Converter)
; If the Microsoft Camera Codec pack is installed, full size camera RAW files can be read with WIC
; Add the file endings of the raw files to view here, e.g.
; FilesProcessedByWIC=*.wdp;*.hdp;*.jxr;*.nef
FilesProcessedByWIC=*.wdp;*.hdp;*.jxr

; File endings of camera RAW files to be searched for embedded JPEG thumb images to display
; Reading just these embedded JPEGs is much faster than decoding the RAW using WIC
FileEndingsRAW=*.pef;*.dng;*.crw;*.nef;*.cr2;*.mrw;*.rw2;*.orf;*.x3f;*.arw;*.kdc;*.nrw;*.dcr;*.sr2;*.raf

; If true, reloads the currently displayed image automatically when it is changed by an external program on disk.
; Also reloads the image list when a file in the current directory is added or deleted.
; Set to false to turn off this behavior.
ReloadWhenDisplayedImageChanged=true

; Background color, R G B, each component must be in [0..255], e.g. "128 128 128" for a middle gray
BackgroundColor=0 0 0

; Color used for transparent parts of images, R G B format as used by BackgroundColor
TransparencyColor=0 0 0

; GUI colors, R G B format as used by BackgroundColor
GUIColor=243 242 231
HighlightColor=255 205 0
SelectionColor=255 205 0
SliderColor=255 0 80
FileNameColor=255 255 255

; GUI font, format: "font name" fontSizeInPoints [bold]
; 'Default' for the default GUI font of Windows
; Example: DefaultGUIFont="Arial" 9.0 bold
DefaultGUIFont=Default

; Contrast correction to apply to all images. Must be in -0.5 .. 0.5
; Values > 0 increase contrast, values < 0 decrease contrast
Contrast=0.0

; Gamma correction to apply to all images. Must be between 0.5 and 2
; Use gamma<1 to increase brightness and gamma>1 to decrease brightness
Gamma=1.0

; Color saturation to apply to all images. Must be in 0.0 .. 2.0
; 0.0 means gray scale image, 1.0 no additional color saturation, 2.0 maximal saturation
Saturation=1.0

; Sharpening to apply for downsampled images. Must be in 0 .. 0.5
; Note that for 100 % zoom, the BestQuality filter will not apply any sharpening, only the other filters do
Sharpen=0.3

; Default parameters for unsharp masking: Radius Amount Threshold
; Note that no unsharp masking can be applied automatically to every image - this setting only provides the default parameters
; when entering the unsharp mask mode
UnsharpMaskParameters=1.0 1.0 4.0

; Default parameters for controlling rotation and perspective correction
RTShowGridLines=true
RTAutoCrop=true
RTPreserveAspectRatio=true

; Default color balance. Negative values for C,M,Y correction, positive for R,G,B.
; Values must be in -1.0 .. +1.0
CyanRed=0.0
MagentaGreen=0.0
YellowBlue=0.0

; Set to true to use high quality sampling as default.
HighQualityResampling=true

; Start in full screen or windowed mode
; 'true' or 'false' to always start in full screen, respectively windowed mode
; 'auto' to choose best mode depending on image size of first image - windowed when it is small, full screen when it is large
ShowFullScreen=false
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

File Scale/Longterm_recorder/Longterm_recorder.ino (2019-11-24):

/* 
 Example using the SparkFun HX711 breakout board with a scale
 By: Nathan Seidle
 SparkFun Electronics
 Date: November 19th, 2014
 License: This code is public domain but you buy me a beer if you use this and we meet someday (Beerware license).

 This example demonstrates basic scale output. See the calibration sketch to get the calibration_factor for your
 specific load cell setup.

 This example code uses bogde's excellent library:"https://github.com/bogde/HX711"
 bogde's library is released under a GNU GENERAL PUBLIC LICENSE

 The HX711 does one thing well: read load cells. The breakout board is compatible with any wheat-stone bridge
 based load cell which should allow a user to measure everything from a few grams to tens of tons.
 Arduino pin 2 -> HX711 CLK
 3 -> DAT
 5V -> VCC
 GND -> GND

 The HX711 board can be powered from 2.7V to 5V so the Arduino 5V power should be fine.

*/

#include "HX711.h"
#define DOUT  3
#define CLK  2

#define calibration_factor -22500.0 //This value is obtained using the SparkFun_HX711_Calibration sketch (or just by testing weights in this program and adjusting)

const byte num_readings = 20;
const byte num_avgs = 20;
const int start_delay = 30000;
const int dump_time = 500;
const float sensitivity = 0.02;

boolean find_weight;
unsigned long counter;
unsigned long last_trigger;
unsigned long now_time;
unsigned long then_time;
float last_readings[num_readings];
float last_avgs[num_avgs];
float reading;
float avg;
float sum;
float delta;
float item_weight;
float prev_avg;

HX711 scale;

void take_reading() {
  reading = scale.get_units();
  sum -= last_readings[counter % num_readings];
  sum += reading;
  avg = sum / num_readings;
  delta = avg - last_avgs[counter % num_avgs];
}

void detect_food() {
  if (delta > sensitivity && find_weight == false) {
    //Serial.println();
    //Serial.print("\t\tfood added: ");
    prev_avg = last_avgs[counter % num_avgs];
    find_weight = true;
    item_weight = delta;
    last_trigger = millis();
  }
}

void measure_weight() {
  if (find_weight) {
    if (delta > sensitivity) { last_trigger = millis(); }
    if (long(millis() - last_trigger) < dump_time) {
      if (avg - prev_avg > item_weight) { item_weight = avg - prev_avg; }
    } else {
      //Serial.print(item_weight * 1000, 2); Serial.print(" g");
      //Serial.println();
      //Serial.println();
      find_weight = false;
      reset_readings();
    }
  }
}

void reset_readings() {
  for (int i = 0; i < num_readings; i++) {
    last_readings[i] = reading;
    last_avgs[i] = reading;
  }
  sum = reading * num_readings;
}

void setup() {
  Serial.begin(9600);

  scale.begin(DOUT, CLK);
  scale.set_scale(calibration_factor); //This value is obtained by using the SparkFun_HX711_Calibration sketch
  //scale.tare(); //Assuming there is no weight on the scale at start up, reset the scale to 0

  Serial.println("Initializing...");
  for(int i = 0; i < 80; i++) {
    Serial.print("|");
    scale.get_units();
    delay(start_delay / 80);
  }
  //Serial.println();
  scale.tare();
  reading = scale.get_units();
  reset_readings();
  //Serial.print("Release the crackers!");
  //Serial.println();
  //Serial.println();
  Serial.println("Time (h),Reading (kg),Average (kg),Delta (g)");

}

void loop() {

  take_reading();
  detect_food();
  measure_weight();
/*
  if (counter % 50 == 0 && not find_weight) {
    Serial.print("total weight: "), Serial.print(avg); Serial.print(" kg");
    Serial.println();
  }
  */
  Serial.print(avg, 4); Serial.print("\t");
  Serial.println(delta, 4);
  
  //Stuff To print for diagnosis
  /*
  now_time = millis();
  if (now_time - then_time > 500 & now_time % 1000 < 500) {
    then_time = now_time;
    //Serial.print(float((unsigned long)(now_time / 1000)) / 3600, 4); Serial.print(",");
    //Serial.print("Reading: ");
    //if (reading > 0) { Serial.print(" "); }
    Serial.print(reading, 4); Serial.print(","); //Serial.print(" kg");
    //Serial.print("   Moving avg: ");
    //if (avg > 0) { Serial.print(" "); }
    Serial.print(avg, 4); Serial.print(","); //Serial.print(" kg");
    //Serial.print("   Delta: ");
    //if (delta > 0) { Serial.print(" "); }
    Serial.print(delta * 1000, 1); //Serial.print(" g");
    Serial.println();
  }
  */
  
  last_readings[counter % num_readings] = reading;
  last_avgs[counter % num_avgs] = avg;
  counter++;  
  
}

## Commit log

2019-10-25 adjust calibration, add total weight reporting
2019-10-25 add sample data and a python script
2019-10-26 write long-term sampler
    [sample_2.csv]
2019-10-26 15 hr sample
    [no weight 15 hours.csv, sample_2.csv]
2019-10-29 Add 51-hr long sample
2019-10-31 Add loaded sample
    [50 kg 24 hours.csv]
2019-10-31 Add camera testing code
2019-11-07 Add main Raspberry Pi programs
2019-11-14 initial 3D printing files
    [Bottom Bracket + camera bottom thingy.0004.ipt, Bottom Bracket + camera bottom thingy.ipt, Bottom Bracket.stl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]
2019-12-01 Change reset method and clearing
    [food_detector.ino, logger.py, photo_stream.py]
2019-12-01 adjust check interval and fix os.remove errors
    [food_detector.ino, logger.py, photo_stream.py]
2019-12-02 reorganize 3d printed parts
    [Bottom Bracket + camera bottom thingy.0004.ipt, Bottom Bracket 2.stl, Bottom Bracket.ipt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]
2019-12-02 fix overlapping food detection and weight checks
    [logger.py]
2019-12-13 Created a python script that displays pictures, prompts the user for a grade, stores that grade in a dictionary then displays the next picture. Currently, it only writes to the csv file at the end of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
    [log.csv]
2019-12-15 move data to google drive
    [log.csv]
2020-01-13 remove data; now on Drive
    [log.csv]
2020-01-13 started sorting program
    [Set_0_all_grades_1.csv, Set_0_all_grades_2.csv, Set_0_all_grades_3.csv]
2020-01-13 add distributions
    [Set_0_all_grades_resolved.csv]
2020-01-14 add intra-rater consistency ratings
    [Set_0_all_grades_1.csv, Set_0_all_grades_2.csv, Set_0_all_grades_3.csv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]
2020-01-14 add hard drive version of flash-drive (GRADER0)
    [Set_0_all_grades_1.csv, Set_0_all_grades_2.csv, Set_0_all_grades_3.csv]
2020-01-17 weight tracking program
    [daily_weights.csv, log_2019-12-01.csv, log_2019-12-13_revised.csv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]
2020-01-18 fix bugs in RPi programs
    [food_detector.ino, logger.py, photo_stream.py]
2020-01-18 fix Arduino < error
    [food_detector.ino, logger.py]
2020-01-18 Setting up arduino code for having multiple scales. Python code will need to be updated still.
2020-01-19 start revising python for 3 scales
    [daily_weights.csv, log_2019-12-01_just_one_day.csv]
2020-01-21 add backtracking to human grader
    [Set_0_all_grades_1.csv, Set_0_all_grades_2.csv, Set_0_all_grades_3.csv]
2020-02-08 adjust wait time for bin replacement
    [multi_scale_sensor.ino]
2020-02-26 improving cluster
    [log.csv, log_2020-02-25.csv]
2020-02-28 basic working EVERYTHING!!!
    [log.csv, log_2020-02-25.csv, pyvenv.cfg]
2020-03-19 adding cluster backups
    [log.csv, log_2020-03-08.csv]
2020-05-12 final stuff from senior year
    [Before_After Comparisons.xlsx]
